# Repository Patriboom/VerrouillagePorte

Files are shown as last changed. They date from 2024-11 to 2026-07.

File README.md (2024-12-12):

# VerrouillagePorte
Verrouillage électronique d'une porte battante.  Projet basé sur programmation Arduino et module Rasp PI pico

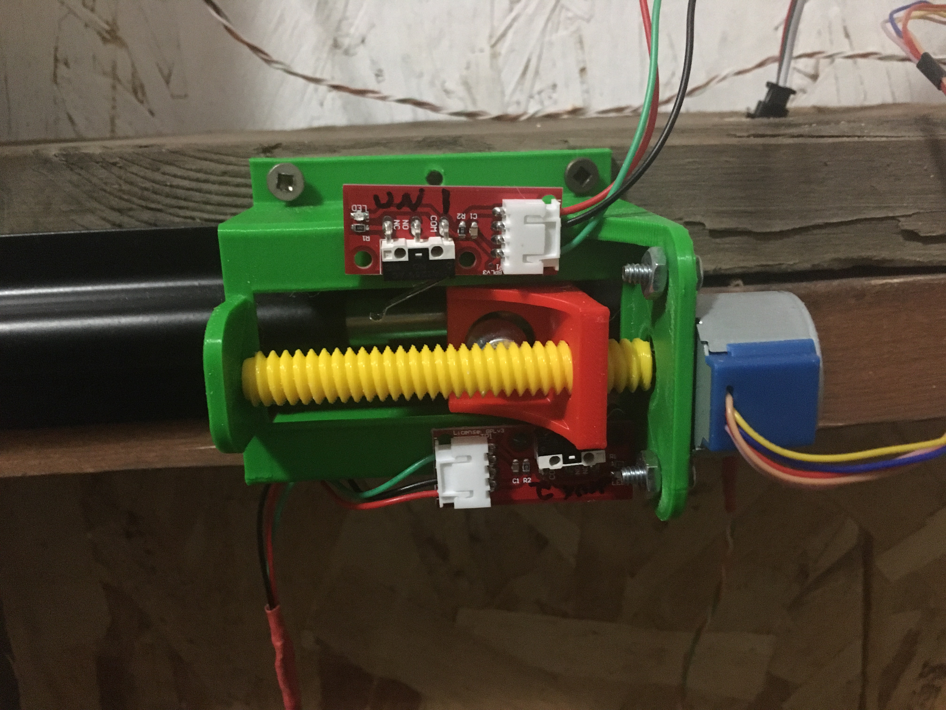
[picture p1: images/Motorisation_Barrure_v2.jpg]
Verrou installé
 Vue d`une installation fonctionnelle

Référez-vous à notre [tutoriel](https://github.com/Patriboom/VerrouillagePorte/tree/main/docs) :

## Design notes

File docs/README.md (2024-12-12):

# Bienvenue!

Dans ce tutoriel, je compte vous montrer comment j'ai imprimé, assemblé et programmé la fermeture et l'ouverture d'une verrou ordinaire qu'on trouve en quincaillerie.

Oui, vous pouvez acheter des produits tout faits, mais vous n'aurez pas la satisfaction de la réalisation personnelle, satisfaction qui me pousse aujourd'hui à vous partager mes fichiers et informations.

# Table des matières

1. [Introduction et présentation](01_Introduction_Presentation.md)
2. [Liste du matériel, des bibliothèques et des outils nécessaires](02_MaterielNecessaire.md)
3. [Le montage sur carte](03_Montage.md)
4. [Le câblage](04_Cablage.md)
5. [L'assemblage](05_Assemblage.md)
6. [Impression du support spécialisé](06_Impression_3d.md)
7. [La programmation](07_Programmation.md)
8. [Premier test et ajustements](08_PremierTest.md)
9. [Félicitations!](09_Felicitations.md)

Voici la pièce centrale du système: le support avec son moteur et ses pièces mobiles.
Verrou installé Vue d'une installation fonctionnelle

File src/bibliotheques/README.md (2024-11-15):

Attention, les bibliothèques fournies ici peuvent être désuètes.

Avec Arduino-IDE, vous trouverez les mêmes bibliothèques, mises à jour et entretenues par leurs auteurs.  Préférez cette option

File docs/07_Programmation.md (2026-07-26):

# 7. Programmation
La programmation est basée sur [Arduino](https://www.arduino.cc/).  L'outils ArduinoIDE est bien connu, répandu et docummenté.
Le code tout entier est disponible dans la banque de bibliothèques de ArduinoIDE.

Ici, je vous explique les différentes parties du code afin que vous puissiez le comprendre ou l'adapter à vos besoins.
Au travers du code, vous trouverez une foule de commentaires et même des repères et vérifications envoyés à la console afin que vous puissiez superviser la progression de la mise en oeuvre en direct.  Je ne reproduira pas ici les commentaires du code.

## Appel des bibliothèques nécessaires
```
	  #include <Stepper.h>
	  #include <SPI.h>
	  #include <MFRC522.h>
```

## Définition des variables de contrôle
```
	  int delai = 60000;
	  int pas = 20;
	  int sens = 1;
	  int vitesseMax = 700;
	  String libre = "oui";
	  bool tourne = false;
	  bool initOUV = false;
	  bool initFER = false;
	  int compteLOW = 0;
	  int compteDEL = 0;
	  int pinSW1 = 27;
	  int pinSW2 = 26;
	  int pinMO1 = 2;
	  int pinMO2 = 3;
	  int pinMO3 = 4;
	  int pinMO4 = 5;
	  int pinDER = 13;
	  int pinDEV = 14;
	  int pinDEB = 15;
	  int pinBOUT = 22;
	  byte CRT_RST = 21;
	  byte CRT_SSC = 17;
```

## Définition des variables de travail
```
 int rendu = 0;
```

## Création des objets
```
	  Stepper moteur(32, pinMO1, pinMO3, pinMO2, pinMO4);
	  MFRC522 cartes(CRT_SSC, CRT_RST);
```

## Définitions communes (setup)
```
	  void setup() {
	    Serial.begin(115200);
	    delay(1550);
	    Serial.println("");
	    Serial.println("Bonjour à vous; voici vos informations de suivi ... ");
	    SPI.begin();              // Init SPI bus
	    Serial.println("SPI est démarré.");
	    cartes.PCD_Init(); // Init each MFRC522 card
	    cartes.PCD_DumpVersionToSerial();
	    Serial.println("---------------------------------------");
	    pinMode(pinSW1, INPUT);   //Interrupteur fermé lorsque la porte est ouverte  => DEL vert
	    pinMode(pinSW2, INPUT);   //Interrupteur fermé lorsque la porte est fermée   => DEL rouge
	    pinMode(pinMO1, OUTPUT);  //Moteur 1
	    pinMode(pinMO2, OUTPUT);  //Moteur 2
	    pinMode(pinMO3, OUTPUT);  //Moteur 3
	    pinMode(pinMO4, OUTPUT);  //Moteur 4
	    pinMode(pinDER, OUTPUT);  //rouge de la DEL
	    pinMode(pinDEV, OUTPUT);  //vert de la DEL
	    pinMode(pinDEB, OUTPUT);  //bleu de la DEL
	    pinMode(pinBOUT, INPUT);
	    digitalWrite(pinMO1, LOW);
	    digitalWrite(pinMO2, LOW);
	    digitalWrite(pinMO3, LOW);
	    digitalWrite(pinMO4, LOW);
	    digitalWrite(pinDER, HIGH);
	    digitalWrite(pinDEV, HIGH);
	    digitalWrite(pinDEB, HIGH);
	    delay(1000);
	    if (digitalRead(pinSW1) == digitalRead(pinSW2)) {
	      Serial.println("Nous avons trouvé le verrou en position médiane; nous ouvrons la porte.");
	      mouvonsMoteur(-1, "fermons");
	    }
	    Serial.println("Voici que tout est défini.  Il ne reste qu`à jouer de la porte.");
	  }  // fin de setup()
```

## Traitement en boucle (loop)
```
	  void loop() {
	    rendu = rendu + 1;
	    if (rendu < 100 && libre == "oui") {
	      digitalWrite(pinDER, HIGH);
	      digitalWrite(pinDEV, LOW);
	      digitalWrite(pinDEB, LOW);
	    } else if (rendu < 200 && libre == "oui") {
	      digitalWrite(pinDER, HIGH);
	      digitalWrite(pinDEV, HIGH);
	      digitalWrite(pinDEB, LOW);
	    } else if (rendu < 300 && libre == "oui") {
	      digitalWrite(pinDER, LOW);
	      digitalWrite(pinDEV, HIGH);
	      digitalWrite(pinDEB, LOW);
	    } else if (rendu < 400 && libre == "oui") {
	      digitalWrite(pinDER, LOW);
	      digitalWrite(pinDEV, HIGH);
	      digitalWrite(pinDEB, HIGH);
	    } else if (rendu < 500 && libre == "oui") {
	      digitalWrite(pinDER, LOW);
	      digitalWrite(pinDEV, LOW);
	      digitalWrite(pinDEB, HIGH);
	    } else if (rendu < 600 && libre == "oui") {
	      digitalWrite(pinDER, HIGH);
	      digitalWrite(pinDEV, LOW);
	      digitalWrite(pinDEB, HIGH);
	    } else {
	      rendu = -1;
	      Serial.println("Nous voici en début de boucle.");
	    }
	    if (libre != "oui") { return; }
	    compteLOW = (digitalRead(pinBOUT) == HIGH) ? ++compteLOW : 0;
	    if (compteLOW > 10 ) { compteLOW = 0; mouvonsMoteur(0, ""); }
	    if ( (!cartes.PICC_IsNewCardPresent() || !cartes.PICC_ReadCardSerial())) {
	      return;
	    } else if (carteValide(cartes.uid.uidByte, cartes.uid.size)) {
	      mouvonsMoteur(0, "");
	    }
	  } //Fin de loop()
```

### Contrôle de la validité de la carte
```
	  bool carteValide(byte *buffer, byte bufferSize) {
	    Serial.print  ("Carte présente et lisible; voici sa valeur : ");
	    String pat = "";
	    for (byte i = 0; i < bufferSize; i++) {
	      pat = pat + String(buffer[i] < 0x10 ? " 0" : " ");
	      pat = pat + String(buffer[i], HEX);
	    }
	    pat.toUpperCase();
	    pat.trim();
	    if (pat == "") { Serial.println(" nulle."); return false; }
	    Serial.print  (pat);
	      for (byte i = 0; i < cartes.uid.size; i++) {
	        cartes.uid.uidByte[i] = 0;
	      }
	    if (pat=="89 A3 F0 97") { Serial.println(" (valide)."); return true; }
	    if (pat=="D3 B8 BD 38") { Serial.println(" (valide)."); return true; }
	    if (pat=="72 67 B1 AB") { Serial.println(" (valide)."); return true; }
	    Serial.println(" --- non valide.");
	    return false;
	  }
```

### Mouvement du moteur
```
	  void mouvonsMoteur(int Sens, String SensMvt) {
	    libre = (Sens == 0) ? "ouvrons" : SensMvt;
	    sens = (Sens == 0) ? 1 : Sens;
	    Serial.println("Activons les mouvements du moteur");
	    if (digitalRead(pinSW2) == LOW) {
	      sens = -1;
	      libre = "fermons";
	    }
	    digitalWrite(pinDER, HIGH);
	    digitalWrite(pinDEV, HIGH);
	    digitalWrite(pinDEB, HIGH);
	    if (Sens != 0) {
	        for (int x=0; x<5; x++) {
	            digitalWrite(pinDEB, LOW);
	            delay(250);
	            digitalWrite(pinDEB, HIGH);
	            delay(250);
	        }
	    }
	    Serial.print  ("État de la situation: ");
	    Serial.print  ((libre == "ouvrons") ? "Femeture demandée. " : "Ouverture demandée. ");
	    if (libre == "ouvrons") {
	      digitalWrite(pinDER, LOW);
	      digitalWrite(pinDEV, HIGH);
	    } else {
	      digitalWrite(pinDER, HIGH);
	        digitalWrite(pinDEV, LOW);
	    }
	    digitalWrite(pinDEB, LOW);
	    Serial.print  ("\tVitesse du moteur: ");
	    Serial.print  (vitesseMax);
	    Serial.print  ("\tPas du moteur: ");
	    Serial.println(pas);
	    int tours = 1;
	    int vitesse = 100;
	    //Mouvement
	    while (libre == "ouvrons" || libre == "fermons") {
	      if (tours/2500 == round(tours/2500) && vitesse < vitesseMax ) {
	        ////Accéléeration du moteur
	        vitesse = vitesse+50; moteur.setSpeed(vitesse);
	      }
	      ////Fin de course atteinte, on met un terme au movement.
	      if ((digitalRead(pinSW2) == LOW && libre == "ouvrons") || (digitalRead(pinSW1) == LOW && libre == "fermons")) {libre = "annoncons"; }
	      moteur.step(sens * pas);
	      delay(10);
	      tours=tours+1;
	    }
	    //Mise au repos du moteur
	    digitalWrite(pinMO1, LOW);
	    digitalWrite(pinMO2, LOW);
	    digitalWrite(pinMO3, LOW);
	    digitalWrite(pinMO4, LOW);
	    //Indication de l'état du verrou
	    digitalWrite(pinDER, HIGH);
	    digitalWrite(pinDEV, HIGH);
	    digitalWrite(pinDEB, HIGH);
	    for (int x=0; x<5; x++) {
	      if (digitalRead(pinSW1) == HIGH) {
	        ////La porte peut être ouverte
	        digitalWrite(pinDER, LOW);
	        Serial.println("Porte verrouilée; partez l`esprit tranquille, car votre porte est sécurisée.");
	      }
	      if (digitalRead(pinSW2) == HIGH) {
	        ////La porte est verrouillée
	        digitalWrite(pinDEV, LOW);
	        Serial.println("Porte déverrouillée; entrez!");
	      }
	      delay (250);
	      digitalWrite(pinDER, HIGH);
	      digitalWrite(pinDEV, HIGH);
	      delay (250);
	      libre = "oui";
	    }
	    delay(1900);
	    digitalWrite(pinDER, HIGH);
	    digitalWrite(pinDEV, HIGH);
	    digitalWrite(pinDEB, HIGH);
	    libre = "oui";
	  }
```

---
[Impression 3d](06_Impression_3d.md) <<<  [Table des matières](README.md)  >>>  [Premier test](08_PremierTest.md)

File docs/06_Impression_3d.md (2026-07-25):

# 6. Impression 3d en PLA
Le PLA est le plastique de base, celui avec lequel tous les apprentis font leurs premières expériences en impression 3d.  C'est un matériel abordable et convenant parfaitement à nos besoins.

## Description des pièces

## Logiciel de conception
Les pièces ici offertes ont été conçues à l'aide du logiciel [_FreeCad_](https://www.freecad.org/downloads.php)
Le fichier FreeCad suivant comprend toutes les pièces nécessaires:

[Fichiers FreeCad FCStd](../../../tree/main/imprime_3d/FreeCad/)
* [Motorisation_Barrure_v3](../../../tree/main/imprime_3d/FreeCad/Motorisation_Barrure_v3.FCStd)

## Tranchage (logiciel de préparation finale)

Les pièces ici présentées ont été préparée à l'aide du logiciel _Cura_
Les fichiers STL peuvent vous être utiles, mais ce serait étonnant car ils ont été générés spécifiquement pour une imprimante 3d. Or chaque imprimante a ses spécifications.
Il vous sera nécessire, donc, de générer vos propres fichiers STL à l'aide de votre logicition de tranchaage.

[Fichiers STL](../../../tree/main/imprime_3d/stl/)
* [Boulon](../../../tree/main/imprime_3d/stl/Motorisation_Barrure_v3-Boulon.stl)
* [Butoire](../../../tree/main/imprime_3d/stl/Motorisation_Barrure_v3-Butoir.stl)
* [Curseur](../../../tree/main/imprime_3d/stl/Motorisation_Barrure_v3-Curseur.stl)
* [Structure](../../../tree/main/imprime_3d/stl/Motorisation_Barrure_v3-Structure.stl)
* [Boitier_01](../../../tree/main/imprime_3d/stl/Obudowa.stl)
* [Boitier_02](../../../tree/main/imprime_3d/stl/Panel.stl)
* [Boitier_03](../../../tree/main/imprime_3d/stl/klapka.stl)

---

[L'assemblage](05_Assemblage.md)  <<<  [Table des matières](README.md)   >>>   [La programmation](07_Programmation.md)

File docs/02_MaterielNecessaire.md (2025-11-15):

# 2. Liste du matériel, des bibliothèques et outils nécessaires

## Électrique

<table>
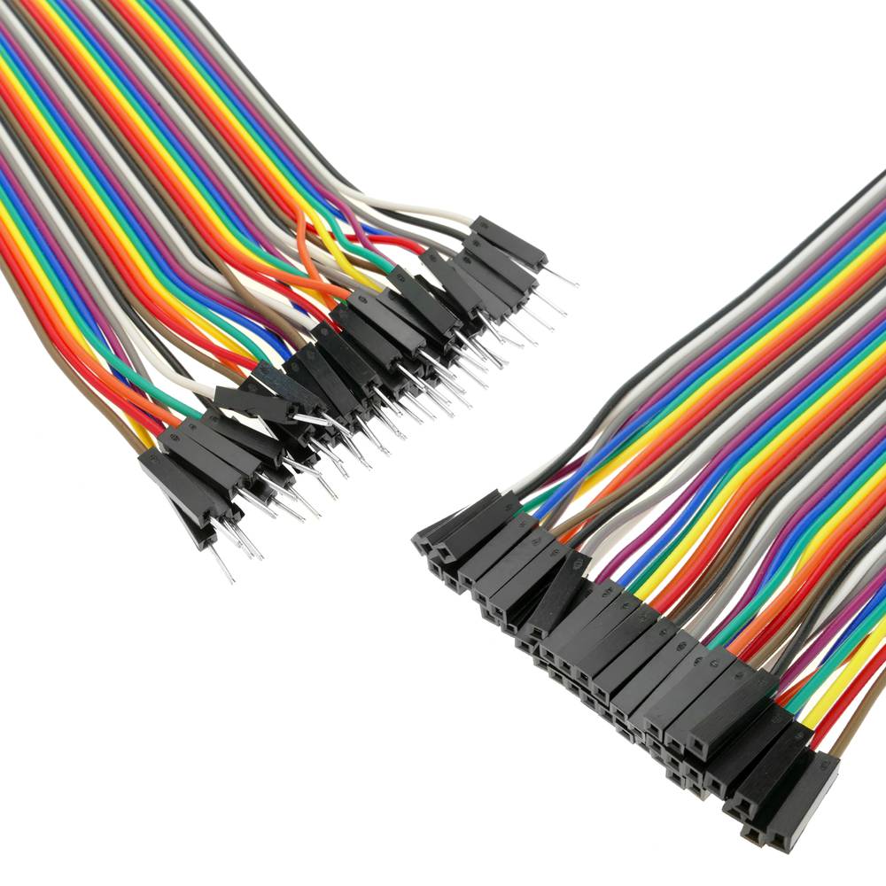
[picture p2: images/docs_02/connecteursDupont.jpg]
	<tr><td>Fils à connecteurs Dupont</td><td></td></tr>
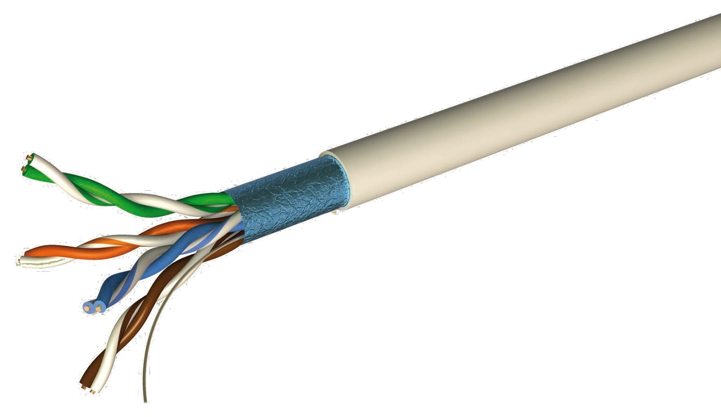
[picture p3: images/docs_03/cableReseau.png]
	<tr><td>Plusieurs sections de fil (un càble réseau peut fournir tout cela, en 8 couleurs)</td><td></td></tr>
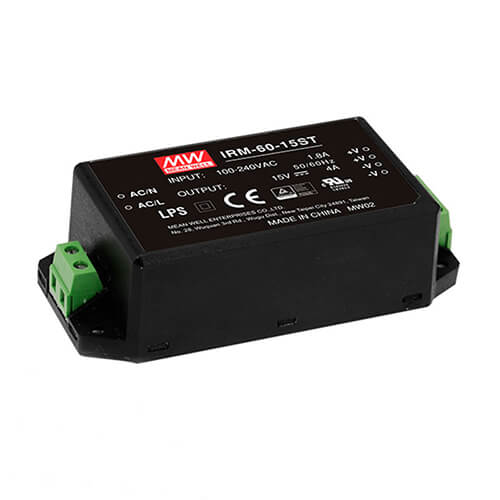
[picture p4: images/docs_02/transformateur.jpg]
	<tr><td>Transformateur 120 VAC -> 5 VDC</td><td></td></tr>
</table>

## Électronique

<table width="100%" border="0">
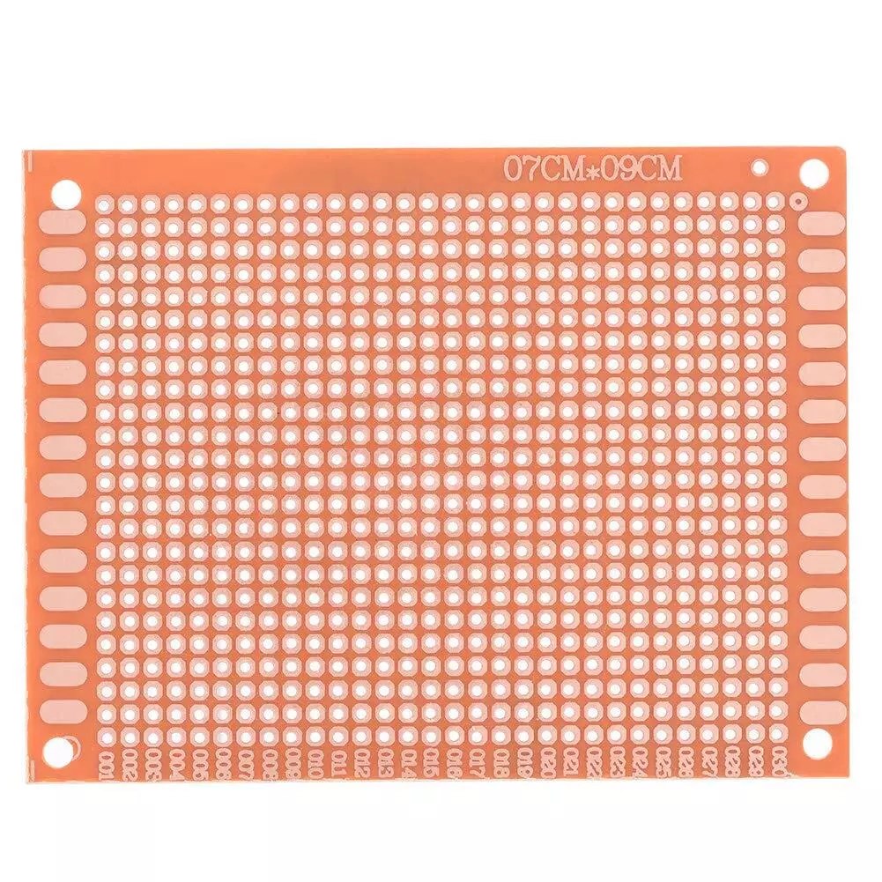
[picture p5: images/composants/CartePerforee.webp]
<tr><td></td><td>Carte perforée aux dimensions appropriées ( au moins 10 par 24 trous espacés de 2.54 mm)</td></tr>
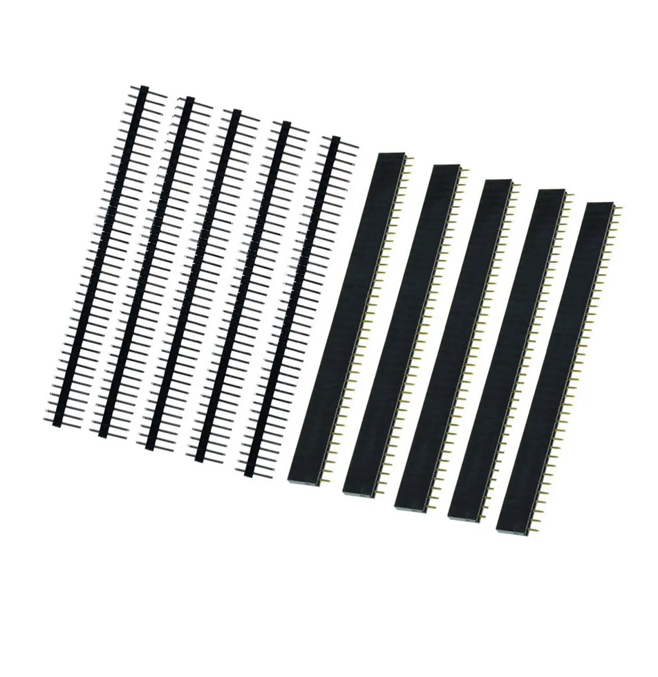
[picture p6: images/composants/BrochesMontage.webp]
<tr><td></td><td>Connecteurs mâles et femelles pour circuit imprimé</td></tr>
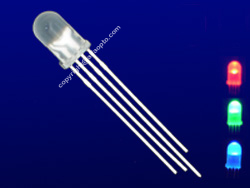
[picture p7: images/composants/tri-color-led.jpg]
<tr><td></td><td>DEL trois couleurs (RVB) à anode commune</td></tr>
<tr><td></td><td> Deux interrupteurs de limite</td></tr>
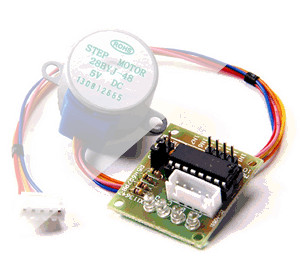
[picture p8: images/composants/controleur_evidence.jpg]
<tr><td> </td><td>Module de pilote de moteur pas à pas ULN2003</td></tr>
<tr><td>Image d'internet: Carte magnétique</td><td>Module RF5 RC522  (lecteur de cartes magnétiques)</td></tr>
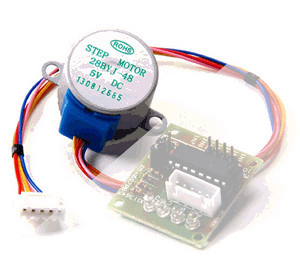
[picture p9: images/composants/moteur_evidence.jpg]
<tr><td></td><td>Moteur pas à pas 28BVJ-48 (5 Volts)</td></tr>
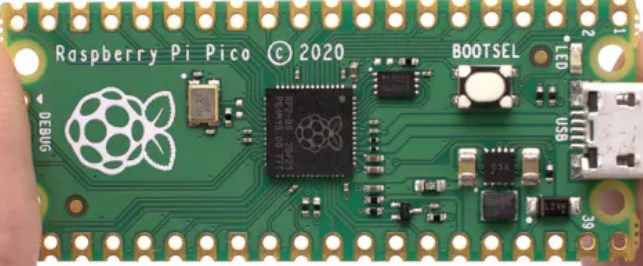
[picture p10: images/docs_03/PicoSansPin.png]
Image d`internet: Rasp PI pico
<tr><td></td><td>Raspberry PI Pico</td></tr>
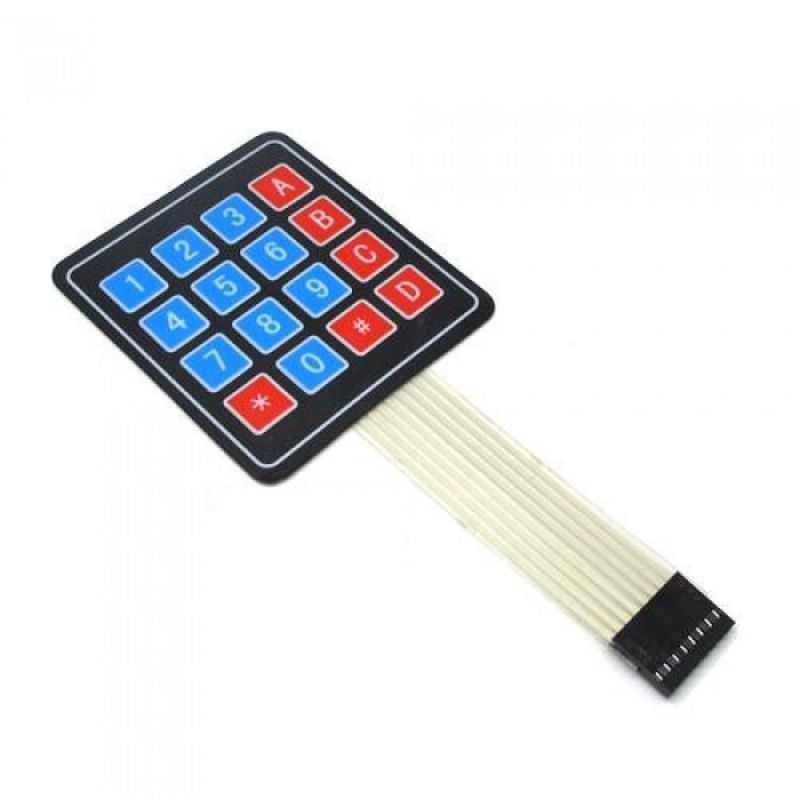
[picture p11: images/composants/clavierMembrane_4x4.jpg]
Image d'internet: Clavier à membrane
<tr><td></td><td>(option clavier à membrane) .. et oui ! ... le clavier à membrane</td></tr>

</table>

## Impression 3d
<table width="100%" border="0">
<tr><td colspan="2">Imprimer les quatre composantes du support en PLA</td></tr>
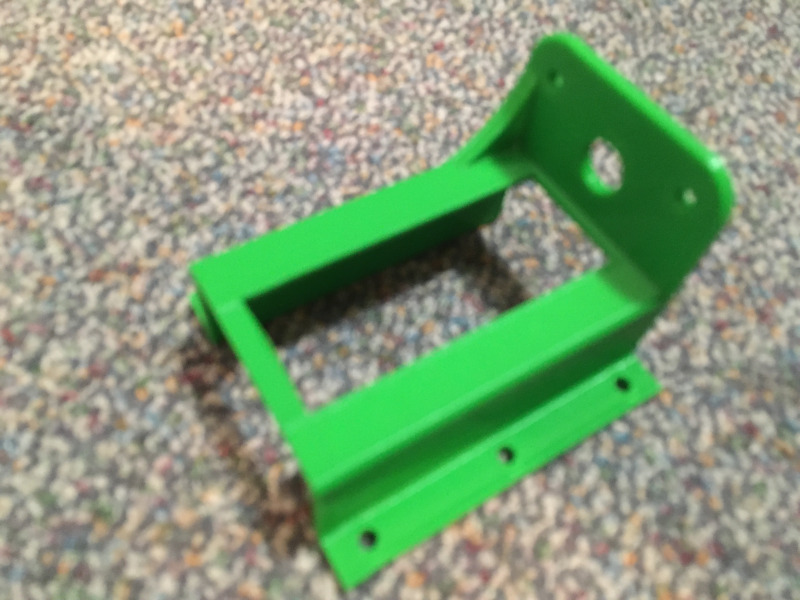
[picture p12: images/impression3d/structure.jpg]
	<tr><td>Une base (structure)</td><td></td></tr>
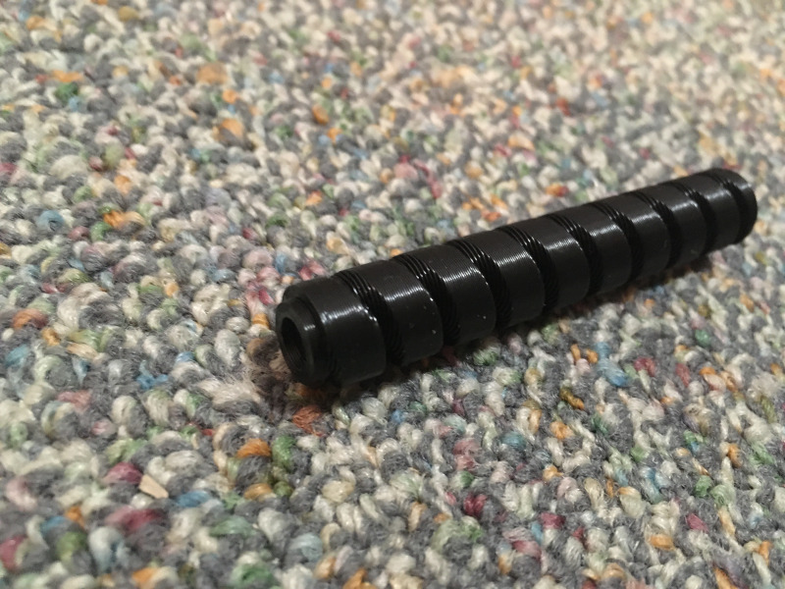
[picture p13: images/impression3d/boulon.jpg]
    <tr><td>Une vis sans fin (boulon)</td><td></td></tr>
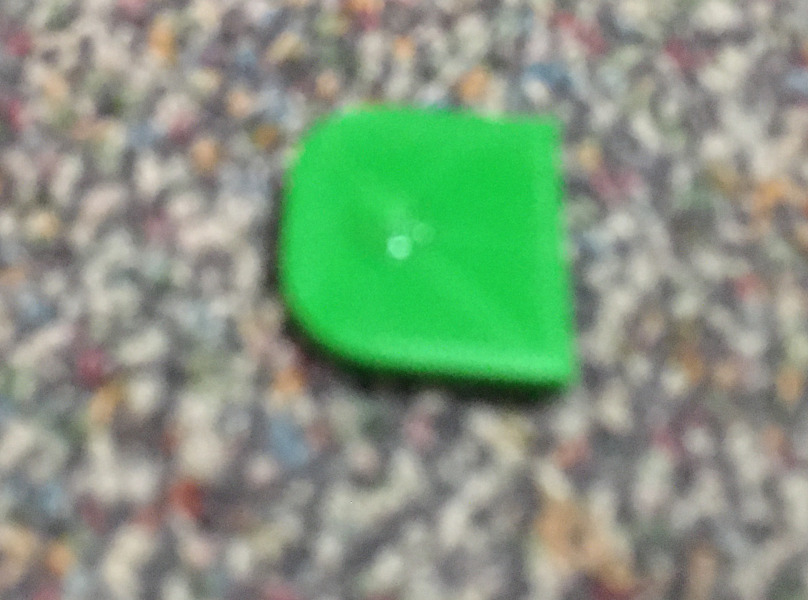
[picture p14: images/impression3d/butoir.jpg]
    <tr><td>Un butoir</td><td></td></tr>
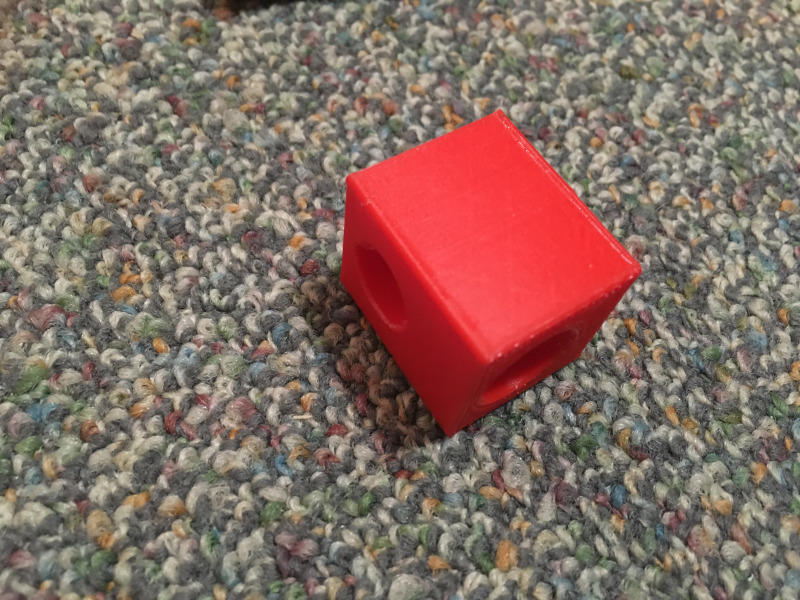
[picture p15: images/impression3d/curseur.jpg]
    <tr><td>Un curseur</td><td></td></tr>
</table>
<br />
<table width="100%" border="0">
<tr><td colspan="2">option: boîtier pour clavier en trois sections<br />C'est ici le modèle gratuitementt par <a href="https://cults3d.com/fr/mod%C3%A8le-3d/gadget/arduino-keypad-4x4-panel" target="_blank">kolec sur cults3d</a>
	</td></tr>
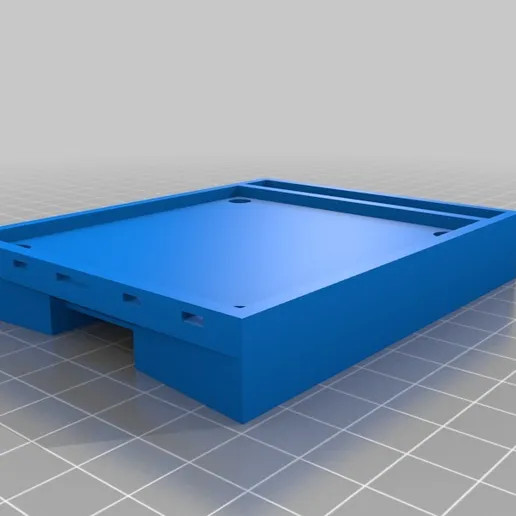
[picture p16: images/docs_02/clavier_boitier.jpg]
    <tr><td>Boîtier</td><td></td></tr>
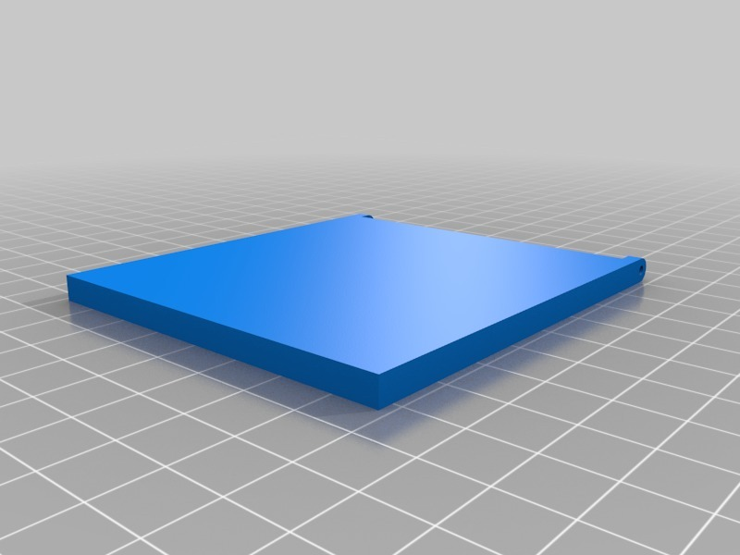
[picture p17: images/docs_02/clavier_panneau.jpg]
    <tr><td>Couvercle</td><td></td></tr>
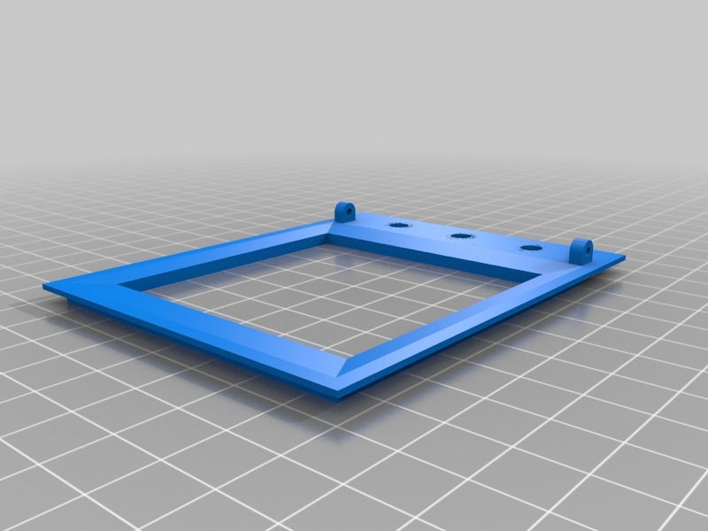
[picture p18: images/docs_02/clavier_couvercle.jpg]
	<tr><td>Dessus</td><td></td></tr>
</td></tr>
</table>

## Informatique
* Éditeur et compilateur de code [Arduino IDE](https://www.arduino.cc/en/software)
* [Bibliothèques installées](https://github.com/Patriboom/VerrouillagePorte/tree/main/src/bibliotheques):
    * Stepper.h
    * SPI.h
    * MFRC522.h
    * (pour l'option clavier à membrane): Keypad.h
* Pilote de carte: Raspberry PI Pico -> utilisez votre interface Arduino-IDE pour cela

## Mécanique
<table>
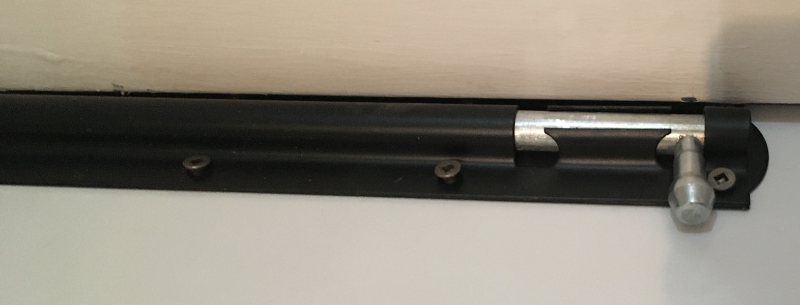
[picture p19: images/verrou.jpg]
<tr><td> </td><td>Verrou</td></tr>
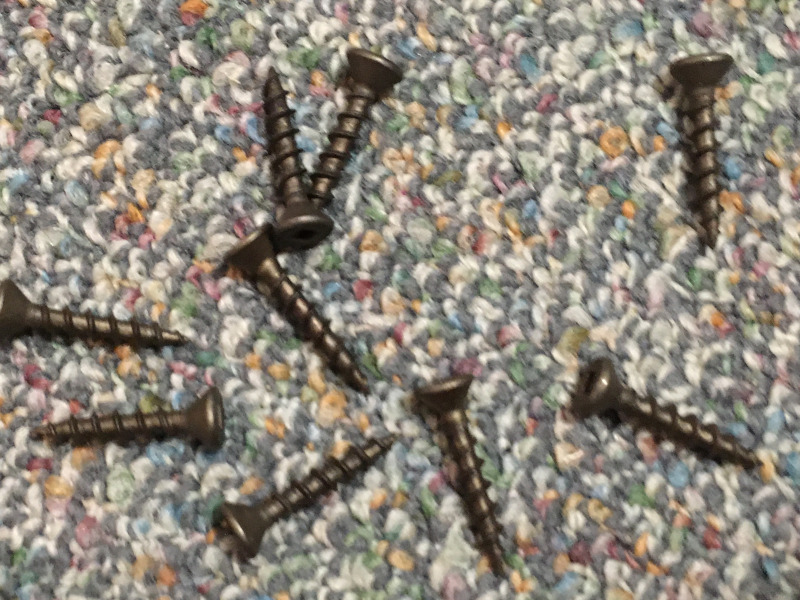
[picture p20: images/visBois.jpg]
<tr><td></td><td>Vis à bois</td></tr>
</table>

## Outils
<table>
	<tr><td></td><td>* Kit à souder  <br />
    &nbsp;&nbsp;&nbsp;&nbsp;&nbsp;&nbsp;- fer à souder <br />
	&nbsp;&nbsp;&nbsp;&nbsp;&nbsp;&nbsp;- étain<br />
		</td></tr>
<tr><td> </td><td>Perceuse & forêts à bois</td></tr>
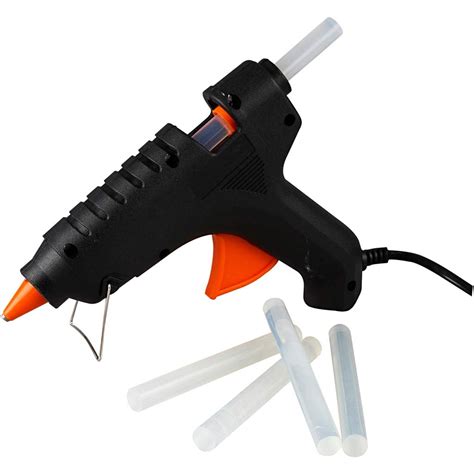
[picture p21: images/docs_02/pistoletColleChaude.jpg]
<tr><td></td><td>Pistolet à colle chaude et colle chaude</td></tr>
<tr></td><td><td>Tous les petits outils habituels permettant de couper et dégainer les fils</td></tr>
<tr><td></td><td>Tourne-vis</td></tr>
</table>

---

[Introduction](01_Introduction_Presentation.md)  <<<  [Table des matières](README.md)   >>>    [Montage](03_Montage.md)

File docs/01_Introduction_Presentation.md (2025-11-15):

# 1.Introduction et présentation du projet
Ma résidence dispose - heureusement en cas d'urgence! - de deux portes d'accès.  Une d'entre elles mène vers un espace commun.  Elle ne pouvait pas être verrouillée.  L'autre mène à l'extérieur et se verrouille à clef.  Cependant, l'installation laisse à désirer; il est facile de forcer la serrure et d'entrer.  Je l'ai d'ailleurs fait à quelques reprises lorsque j'ai oublié ma clef!  Je voulais donc plus de sécurité et la possibilité de me « forcer » à ne pas oublier ma clef avant de partir.

## Présentation

Ce projet a été réalisé avec les composants électroniques que j'avais sous la main.  Bien sûr, il pourrait être meilleur, plus beau ou plus performant, mais ce sont les composants dans je disposais qui ont été assemblés et réunis afin de réaliser une opération utile à la sécurisation de ma résidence.

Sans surprise, la sécurité étant ce qui est visé lors de l'ajout d'un verrou, la sécurité doit aussi être visée lors de sa motorisation.  L'image ci-bas montre les composants AVANT la finition esthétique de la porte, ceux-ci étant installés dans la structure même de la porte.
<br clear="all">

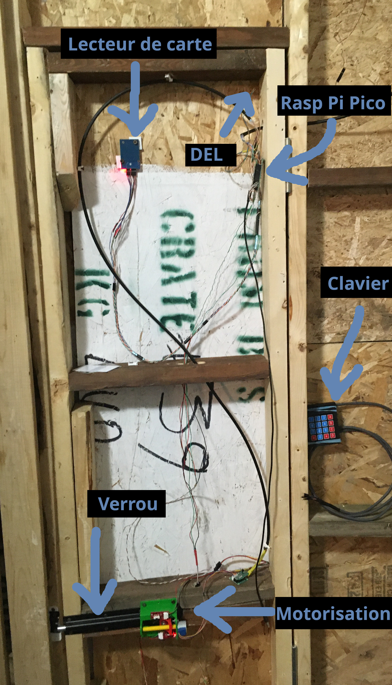
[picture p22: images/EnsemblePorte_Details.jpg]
Avant finition de la porte

<br clear="all">

## Fonctionnement
Ce système est basé sur un Raspberry Pi Pico qui gère l'activation d'un moteur par la lecture d'une carte magnétique.

Image d`internet: Rasp PI pico

Image d'internet: Carte magnétique

Image d'internet: moteur à pas
<br clear="all">
<br clear="all">
Le système est appelé à gérer aussi la vérification d'un code d'accès introduit à l'aide d'un clavier à membrane.
<br clear="all"><br />
Image d'internet: Clavier à membrane
<br clear="all"><br clear="all">
Le système électronique meut la barre d'un verrou en acier, barre d'environ 1cm de diamètre.

-----
[Table des matières](README.md)   >>>  [Le nécessaire](02_MaterielNecessaire.md)

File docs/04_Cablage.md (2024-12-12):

# 4. Le câblage

Prévoyez des câbles de bonne longueur pour chacun des éléments selon le positionnement de ceux-ci dans votre environnement.

De longueurs semblables, vous aurez: 
* Le contrôleur du moteur
* L'interrupteur de position « ouverte »
* L'interrupteur de position « verrouillée »

Quant aux autres, vous devrez composer avec l'environnement de votre installation.

Voici le schéma du câblage.
<br clear="all" />
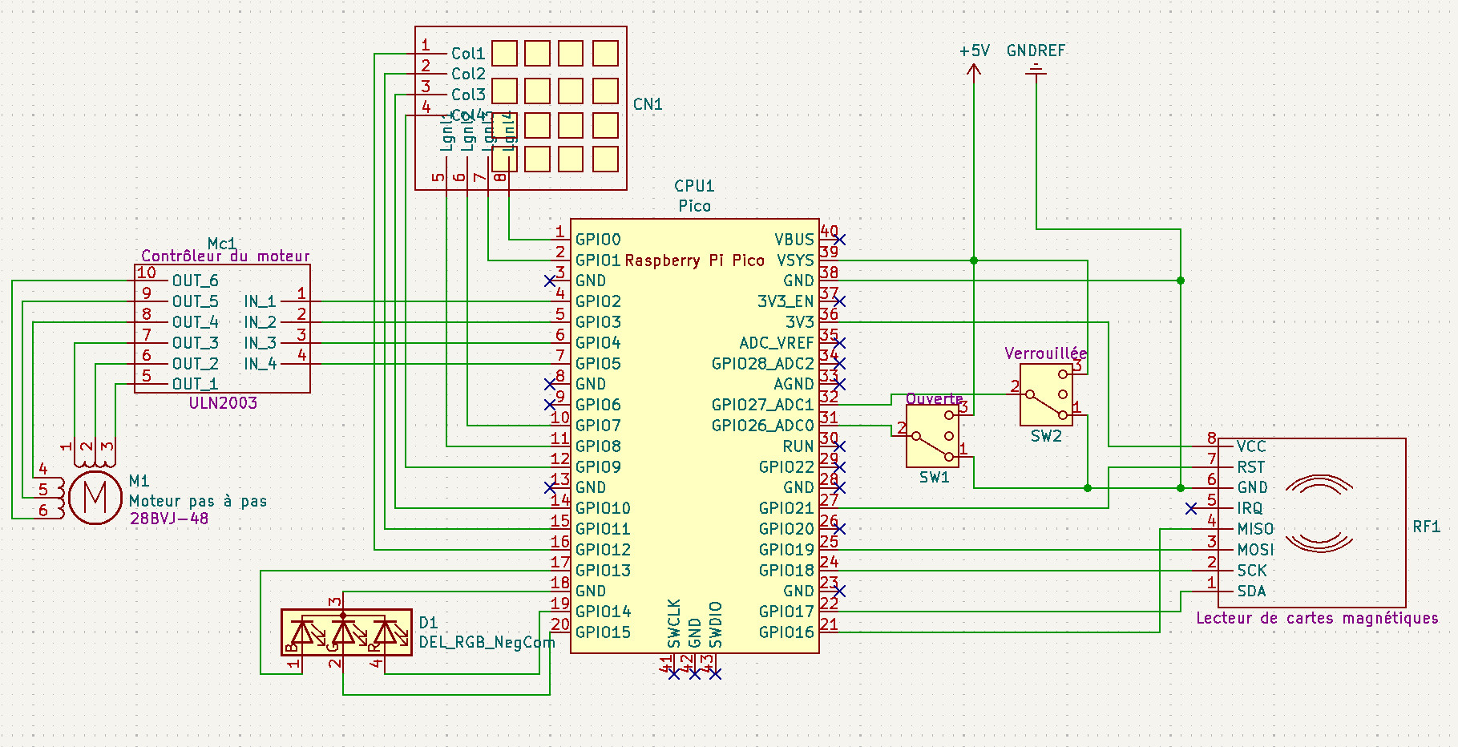
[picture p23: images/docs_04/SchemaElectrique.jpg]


---

[Montage du circuit](03_Montage.md)  <<<  [Table des matières](README.md)   >>>    [L'assemblage](05_Assemblage.md)

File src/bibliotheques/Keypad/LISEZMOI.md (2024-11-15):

# Keypad

Voici la petite bibliothèque servant à exploiter un clavier à membrane

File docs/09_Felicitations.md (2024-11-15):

# 9. Félicitations

---
[Premier test](08_PremierTest.md) <<<  [Table des matières](README.md)

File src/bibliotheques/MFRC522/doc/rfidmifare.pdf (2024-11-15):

## Using a MFRC522 reader to read and write MIFARE RFID cards

on ARDUINO through the MFRC522 library BY COOQROBOT.
Mario Capurso (m.capurso@libero.it)

MIFARE is the NXP Semiconductors-owned trademark of a series of chips widely
used in contactless smart cards and proximity cards. According to the producers, billions of smart card chips and many millions of reader modules have been sold. [1]

The technology is owned by NXP Semiconductors (spin off from Philips Electronics in 2006) with headquarters in Eindhoven, Netherlands, and main business sites in Nijmegen, Netherlands, and Hamburg, Germany.

The MIFARE name covers proprietary technologies based upon various levels of the ISO/IEC 14443 Type A 13.56 MHz contactless smart card standard.
The MIFARE name (derived from the term MIkron FARE Collection System) covers
seven different kinds of contactless cards.

MIFARE Classic employs a proprietary protocol compliant to parts (but not all) of ISO/IEC 14443-3 Type A, with an NXP proprietary security protocol for authentication and ciphering.

The MIFARE Classic card is fundamentally just a memory storage device, where the memory is divided into segments and blocks with simple security mechanisms for access control. They are ASIC-based and have limited computational power. Thanks
to their reliability and low cost, those cards are widely used for electronic wallet, access control, corporate ID cards, transportation or stadium ticketing.

The MIFARE Classic 1K offers 1024 bytes of data storage, split into 16 sectors; each sector is protected by two different keys, called A and B. Each key can be programmed to allow operations such as reading, writing, increasing valueblocks, etc. MIFARE Classic 4K offers 4096 bytes split into forty sectors, of which 32 are same size as in the 1K with eight more that are quadruple size sectors. MIFARE Classic mini offers 320 bytes split into five sectors.

For each of these card types, 16 bytes per sector are reserved for the keys and access conditions and can not normally be used for user data. Also, the very first 16 bytes contain the serial number of the card and certain other manufacturer data and are read only. That brings the net storage capacity of these cards down to 752 bytes for MIFARE Classic 1k, 3440 bytes for MIFARE Classic 4k, and 224 bytes for Mini. It uses an NXP proprietary security protocol (Crypto-1) for authentication and ciphering.

The encryption used by the MIFARE Classic card uses a 48 bit key. [18]
A presentation by Henryk Plötz and Karsten Nohl[19] at the Chaos Communication Congress in December 2007 described a partial reverse-engineering of the algorithm used in the MIFARE Classic chip. Abstract and slides[20] are available online. A paper that describes the process of reverse engineering this chip was published at the August 2008 USENIX security conference.[21] (https://www.usenix.org/legacy/events/sec08/tech/full_papers/nohl/nohl.pdf)

In March 2008 the Digital Security[22] research group of the Radboud University Nijmegen made public that they performed a complete reverse-engineering and
were able to clone and manipulate the contents of an OV-Chipkaart which is a MIFARE Classic card.[23] (http://www.cs.ru.nl/~flaviog/publications/Talk.Mifare.pdf) For demonstration they used the Proxmark device, a 125 kHz / 13.56 MHz research instrument.[24] The schematics and software are released under the free GNU General Public License by Jonathan Westhues in 2007. They demonstrate it is even possible to perform card-only attacks using just an ordinary stock-commercial NFC reader in combination with the libnfc library.

In April 2009 new and better card-only attack on MIFARE Classic has been
found. It was first announced at the Rump session of Eurocrypt 2009.[35] This attack was presented at SECRYPT 2009.[36] The full description of this latest and fastest attack to date can also be found in the IACR preprint archive.[37] The new attack improves by a factor of more than 10 all previous card-only attacks on MIFARE Classic, has instant running time, and it does not require a costly precomputation.

The new attack allows to recover the secret key of any sector of MIFARE Classic card via wireless interaction, within about 300 queries to the card. It can then be combined with the nested authentication attack in the Nijmegen Oakland paper to recover subsequent keys almost instantly. Both attacks combined and with the right hardware equipment such as Proxmark3, one should be able to clone any MIFARE Classic card in not more than 10 seconds. This is much faster than previously thought.

The MFRC522 is a highly integrated reader/writer IC for contactless communication at 13.56 MHz. The MFRC522 reader supports ISO/IEC 14443 A/MIFARE mode.
The MFRC522’s internal transmitter is able to drive a reader/writer antenna designed to communicate with ISO/IEC 14443 A/MIFARE cards and transponders without additional active circuitry. The receiver module provides a robust and efficient implementation for demodulating and decoding signals from ISO/IEC 14443 A/MIFARE compatible cards and transponders. The digital module manages the complete ISO/IEC 14443 A framing and error detection (parity and CRC) functionality.

The MFRC522 supports all variants of the MIFARE Mini, MIFARE 1K, MIFARE 4K, MIFARE Ultralight, MIFARE DESFire EV1 and MIFARE Plus RF identification protocols. To aid readability throughout this data sheet, the MIFARE Mini,

MIFARE 1K, MIFARE 4K, MIFARE Ultralight, MIFARE DESFire EV1 and MIFARE Plus products and protocols have the generic name MIFARE.

The following host interfaces are provided:

- Serial Peripheral Interface (SPI)
- Serial UART (similar to RS232 with voltage levels dependant on pin voltage supply)
- I2C-bus interface

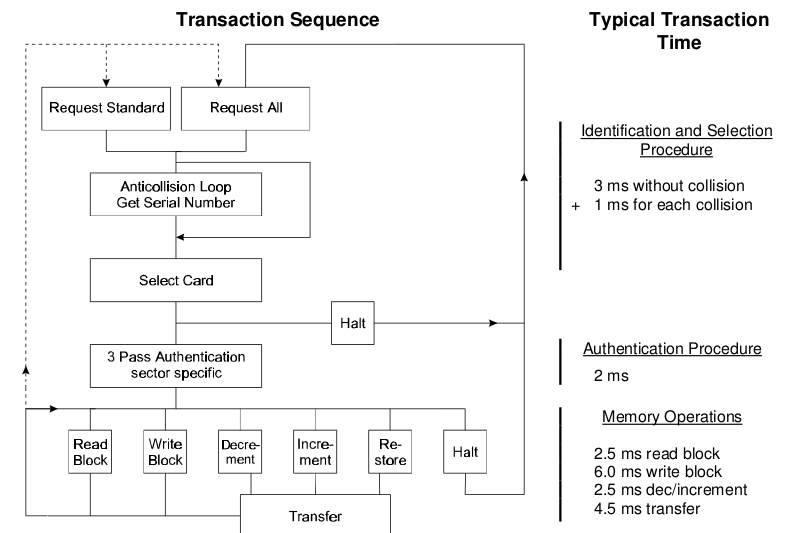
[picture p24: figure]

Answer to Request :

With the Answer to Request sequence the MIFARE® RWD (Read Write Device) requests all MIFARE® cards in the antenna field. When a card is in the operating range of a RWD, the RWD continues communication with the appropriate protocol.

Anticollision loop
In the Anticollision loop the serial number of the card is read. If there are several cards in the operating range of a RWD they can be distinguished by their different serial numbers and one can be selected (Select card) for further transactions. The unselected cards return to the standby mode and wait for a new Answer to Request and Anticollision loop.

Select Card
With the Select Card command the RWD selects one individual card for further authentication and memory related operations. The card returns the Answer to Select (ATS) code, which determines the individual type of the selected card.

Access Specification
After identification and selection of one card the RWD specifies the memory location of the following access.

Three Pass Authentication
The appropriate access key for the previously specified access is used for 3 Pass Authentication. Any communication after authentication is automatically encrypted at the sender and decrypted by the receiver.

Read/Write

After authentication any of the following operations may be performed:

READ | reads one block
WRITE | writes one block
DECREMENT | decrements the contents of one block and stores the result
| in the data-register
INCREMENT | increments the contents of one block and stores the result
| in the data-register
TRANSFER | writes the contents of the data-register to one block
RESTORE | stores the contents of one block in the data-register

The MF1ICS50 IC of a Mifare Classic has integrated a 8192 Bit EEPROM which is split into 16 sectors with 4 blocks. One block consists of 16 bytes (1 Byte = 8 Bit).

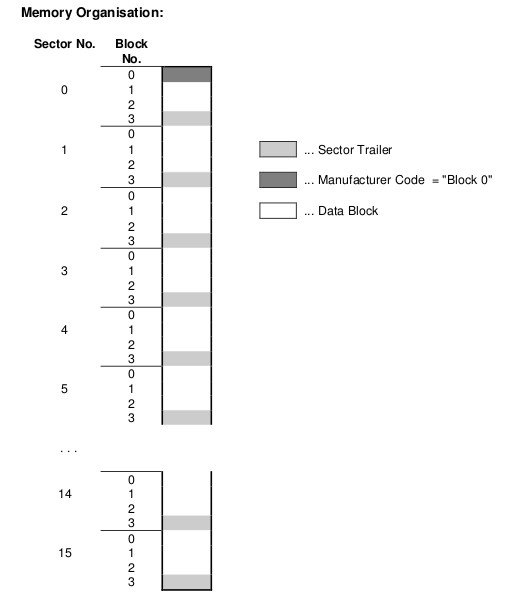
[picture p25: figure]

Manufacturer Code (Block 0 of Sector 0)

The first block of the memory is reserved for manufacturer data like 32 bit serial number. This is a read only block. In many documents it is named "Block 0".

Data Block (Block 0 to 3 except "Block 0")

Access conditions for the Data Blocks are defined in the Sector Trailers. According to these conditions data can be read, written, incremented, decremented, transferred or restored either with Key A, Key B or never.


If Key B may be read in the corresponding Sector Trailer it cannot serve for authentication (all grey marked lines in previous table). Consequences: If the RWD tries to authenticate any block of a sector with key B using grey marked
access conditions, the card will refuse any subsequent memory access after authentication


The described memory organization makes it possible to appoint different sectors to different applications and to prevent data corruption by using application specific secret keys. Keys can only be altered by a RWD which has stored the actual Key A or Key B if this is allowed according to access conditions. Otherwise the actual key cannot be changed anymore.

Before the execution of a command the correct format of the Access Conditions is checked by the Card-IC. Thus, when programming the Sector Trailer the card needs to be fixed within the operating range of a RWD's antenna to prevent interruption of the write operation because any unsuccessful write operation may lead to blocking the whole sector.


## MFRC522.h – A Library to use ARDUINO RFID MODULE KIT 13.56

MHZ BY COOQROBOT.

There are three hardware components involved:

1) The micro controller: An Arduino
2) The PCD (Proximity Coupling Device): NXP MFRC522 Contactless Reader IC
3) The PICC (short for Proximity Integrated Circuit Card): A card or tag using the ISO 14443A interface, eg Mifare or NTAG203.

MIFARE Classic 1K (MF1S503x):

Has 16 sectors * 4 blocks/sector * 16 bytes/block = 1024 bytes. The blocks are numbered 0-63.

Block 3 in each sector is the Sector Trailer.
* | Bytes 0-5: | Key A
* | Bytes 6-8: | Access Bits
* | Bytes 9: | User data
* | Bytes 10-15: Key B (or user data)

Block 0 is read only manufacturer data.

To access a block, an authentication using a key from the block's sector must be performed first.

Example: To read from block 10, first authenticate using a key from sector 3 (blocks 8-11).

All keys are set to FFFFFFFFFFFFh at chip delivery.

Warning: Please read section 8.7 "Memory Access". It includes this text: if the PICC detects a format violation the whole sector is irreversibly blocked.

To use a block in "value block" mode (for Increment/Decrement operations) you need to change the sector trailer. Use PICC_SetAccessBits() to calculate the bit patterns.

Commands sent to the PICC.

The commands used by the PCD to manage communication with several PICCs (ISO 14443-3, Type A, section 6.4)

PICC_CMD_REQA = 0x26,
REQuest command, Type A. Invites PICCs in state IDLE to go to READY and prepare for anticollision or selection. 7 bit frame.
PICC_CMD_WUPA = 0x52,
Wake-UP command, Type A. Invites PICCs in state IDLE and HALT to go to READY(*) and prepare for anticollision or selection. 7 bit frame.
PICC_CMD_CT = 0x88,
Cascade Tag. Not really a command, but used during anti collision. PICC_CMD_SEL_CL1 = 0x93,
Anti collision/Select, Cascade Level 1
PICC_CMD_SEL_CL2 = 0x95,
Anti collision/Select, Cascade Level 2 PICC_CMD_SEL_CL3 = 0x97,
Anti collision/Select, Cascade Level 3
PICC_CMD_HLTA = 0x50,
HaLT command, Type A. Instructs an ACTIVE PICC to go to state HALT.

The commands used for MIFARE Classic
Use PCD_MFAuthent to authenticate access to a sector, then use these commands to read/write/modify the blocks on the sector.
The read/write commands can also be used for MIFARE Ultralight.

PICC_CMD_MF_AUTH_KEY_A = 0x60,
Perform authentication with Key A
PICC_CMD_MF_AUTH_KEY_B = 0x61,
Perform authentication with Key B
PICC_CMD_MF_READ | = 0x30,
Reads one 16 byte block from the authenticated sector of the PICC. Also used for MIFARE Ultralight.
PICC_CMD_MF_WRITE | = 0xA0,
Writes one 16 byte block to the authenticated sector of the PICC. Called "COMPATIBILITY WRITE" for MIFARE Ultralight.
PICC_CMD_MF_DECREMENT = 0xC0,
Decrements the contents of a block and stores the result in the internal data register.
PICC_CMD_MF_INCREMENT = 0xC1,
Increments the contents of a block and stores the result in the internal data register.
PICC_CMD_MF_RESTORE | = 0xC2,
Reads the contents of a block into the internal data register. PICC_CMD_MF_TRANSFER = 0xB0,
Writes the contents of the internal data register to a block.

List of the functions in the library

Functions for setting up the Arduino

MFRC522(byte chipSelectPin, byte resetPowerDownPin);
void setSPIConfig();

Basic interface functions for communicating with the MFRC522

void PCD_WriteRegister(byte reg, byte value);
void PCD_WriteRegister(byte reg, byte count, byte *values);
byte PCD_ReadRegister(byte reg);
void PCD_ReadRegister(byte reg, byte count, byte *values, byte rxAlign = 0); void setBitMask(unsigned char reg, unsigned char mask);
void PCD_SetRegisterBitMask(byte reg, byte mask);
void PCD_ClearRegisterBitMask(byte reg, byte mask);
byte PCD_CalculateCRC(byte *data, byte length, byte *result);

Functions for manipulating the MFRC522

void PCD_Init();
void PCD_Reset();
void PCD_AntennaOn();

Functions for communicating with PICCs

byte PCD_TransceiveData(byte *sendData, byte sendLen, byte *backData, byte *backLen, byte *validBits = NULL, byte rxAlign = 0, bool checkCRC = false);

byte PCD_CommunicateWithPICC(byte command, byte waitIRq, byte *sendData, byte sendLen, byte *backData = NULL, byte *backLen = NULL, byte *validBits = NULL, byte rxAlign = 0, bool checkCRC = false);

byte PICC_RequestA(byte *bufferATQA, byte *bufferSize);
byte PICC_WakeupA(byte *bufferATQA, byte *bufferSize);
byte PICC_REQA_or_WUPA( byte command, byte *bufferATQA, byte *bufferSize); byte PICC_Select(Uid *uid, byte validBits = 0);
byte PICC_HaltA();

Functions for communicating with MIFARE PICCs

byte PCD_Authenticate(byte command, byte blockAddr, MIFARE_Key *key, Uid *uid); void PCD_StopCrypto1();
byte MIFARE_Read(byte blockAddr, byte *buffer, byte *bufferSize);
byte MIFARE_Write(byte blockAddr, byte *buffer, byte bufferSize);
byte MIFARE_Decrement(byte blockAddr, long delta);
byte MIFARE_Increment(byte blockAddr, long delta);
byte MIFARE_Restore(byte blockAddr);
byte MIFARE_Transfer(byte blockAddr);
byte MIFARE_Ultralight_Write(byte page, byte *buffer, byte bufferSize);

Support functions

byte PCD_MIFARE_Transceive( byte *sendData, byte sendLen, bool acceptTimeout = false);
const char *GetStatusCodeName(byte code);
byte PICC_GetType(byte sak);
const char *PICC_GetTypeName(byte type);
void PICC_DumpToSerial(Uid *uid);
void PICC_DumpMifareClassicToSerial(Uid *uid, byte piccType, MIFARE_Key *key);
void PICC_DumpMifareClassicSectorToSerial(Uid *uid, MIFARE_Key *key, byte sector); void PICC_DumpMifareUltralightToSerial();
void MIFARE_SetAccessBits(byte *accessBitBuffer, byte g0, byte g1, byte g2, byte g3);

Convenience functions - does not add extra functionality

bool PICC_IsNewCardPresent();
bool PICC_ReadCardSerial();

Detailed documentation – enum and structures

PICC types we can detect. Remember to update PICC_GetTypeName() if you add more.

enum PICC_Type

Return codes from the functions in this class. Remember to update GetStatusCodeName() if you add more.

enum StatusCode

A struct used for passing the UID of a PICC.

typedef struct {
byte | size; | Number of bytes in the UID. 4, 7 or 10.
byte | uidByte[10];
byte | sak; | The SAK (Select acknowledge) byte returned
| | from the PICC after successful selection.
} Uid

A struct used for passing a MIFARE Crypto1 key

typedef struct {
byte | keyByte[MF_KEY_SIZE];
} MIFARE_Key;

Example:
// Prepare key - all keys are set to FFFFFFFFFFFFh at chip delivery from the factory. MFRC522::MIFARE_Key key;
for (byte i = 0; i < 6; i++) key.keyByte[i] = 0xFF;

Member variables

Uid uid; | Used by PICC_ReadCardSerial().

Detailed documentation – functions

+Create object instance
MFRC522(
byte chipSelectPin, Arduino pin used for SPI chip select byte resetPowerDownPin Arduino pin used for SPI reset
);
Example:
#include <SPI.h>

#include <MFRC522.h>

#define SS_PIN 10 //Arduino Uno

#define RST_PIN 9

MFRC522 mfrc522(SS_PIN, RST_PIN); | // Create MFRC522 instance.

+Initializes the MFRC522 chip.
void MFRC522::PCD_Init()
Example:
void setup() {
Serial.begin(9600); | // Init serial communications with PC
SPI.begin(); | // Init SPI bus
mfrc522.PCD_Init(); | // Init MFRC522 card
}

+Set SPI bus to work with MFRC522 chip.

Please call this function if you have changed the SPI config since the MFRC522 constructor was run.

void MFRC522::setSPIConfig()

+Performs a soft reset on the MFRC522 chip and waits for it to be ready again. void MFRC522::PCD_Reset()

+Turns the antenna on by enabling pins TX1 and TX2.
After a reset these pins are disabled.
void MFRC522::PCD_AntennaOn()

+Transmits a REQuest command, Type A. Invites PICCs in state IDLE to go to READY and prepare for anticollision or selection. 7 bit frame.
Beware: When two PICCs are in the field at the same time I often get STATUS_TIMEOUT -probably due do bad antenna design.
return STATUS_OK on success, STATUS_??? otherwise.
byte MFRC522::PICC_RequestA(
byte *bufferATQA, The buffer to store the ATQA (Answer to request) in
byte *bufferSize Buffer size, at least two bytes. Also number of bytes returned if STATUS_OK.

+Transmits a Wake-UP command, Type A. Invites PICCs in state IDLE and HALT to go to READY(*) and prepare for anticollision or selection. 7 bit frame.
Beware: When two PICCs are in the field at the same time I often get STATUS_TIMEOUT -probably due do bad antenna design.
return STATUS_OK on success, STATUS_??? otherwise.
byte MFRC522::PICC_WakeupA(
byte *bufferATQA, The buffer to store the ATQA (Answer to request) in
byte *bufferSize Buffer size, at least two bytes. Also number of bytes returned if STATUS_OK.

+Transmits SELECT/ANTICOLLISION commands to select a single PICC.
Before calling this function the PICCs must be placed in the READY(*) state by calling PICC_RequestA() or PICC_WakeupA().
On success:

-The chosen PICC is in state ACTIVE(*) and all other PICCs have returned to state IDLE/HALT. (Figure 7 of the ISO/IEC 14443-3 draft.)
-The UID size and value of the chosen PICC is returned in *uid along with the SAK.

A PICC UID consists of 4, 7 or 10 bytes.
Only 4 bytes can be specified in a SELECT command, so for the longer UIDs two or three iterations are used:
UID size | Number of UID bytes | Cascade levels | Example of PICC
======== | =================== | ============== | ===============
single | 4 | 1 | MIFARE Classic
double | 7 | 2 | MIFARE Ultralight
triple | 10 | 3 | Not currently in use?

return STATUS_OK on success, STATUS_??? otherwise.
byte MFRC522::PICC_Select(
Uid *uid, | Pointer to Uid struct. Normally output, but can also
be used to supply a known UID.
byte validBits | The number of known UID bits supplied in *uid.

Normally 0. If set you must also supply uid->size.

Description of buffer structure:

Byte 0: SEL | Indicates the Cascade Level: PICC_CMD_SEL_CL1,
PICC_CMD_SEL_CL2 or PICC_CMD_SEL_CL3
Byte 1: NVB | Number of Valid Bits (in complete command, not just the UID):
High nibble: complete bytes, Low nibble: Extra bits.
Byte 2: UID-data or CT See explanation below. CT means Cascade Tag.
Byte 3: UID-data
Byte 4: UID-data
Byte 5: UID-data
Byte 6: BCC | Block Check Character - XOR of bytes 2-5
Byte 7: CRC_A
Byte 8: CRC_A

The BCC and CRC_A is only transmitted if we know all the UID bits of the current Cascade Level.
Description of bytes 2-5: (Section 6.5.4 of the ISO/IEC 14443-3 draft: UID contents and cascade levels)
UID size | Cascade level | Byte2 Byte3 Byte4 Byte5
======== | ============= | ===== ===== ===== =====
4 bytes | 1 | uid0 uid1 uid2 uid3

7 bytes | 1 | CT | uid0 uid1 uid2
2 | uid3 uid4 uid5 uid6
10 bytes | 1 | CT | uid0 uid1 uid2
| 2 | CT | uid3 uid4 uid5

+Instructs a PICC in state ACTIVE(*) to go to state HALT. return STATUS_OK on success, STATUS_??? otherwise.
byte PICC_HaltA();
Example:
// Halt PICC
mfrc522.PICC_HaltA();

+Executes the MFRC522 MFAuthent command.
This command manages MIFARE authentication to enable a secure communication to any MIFARE Mini, MIFARE 1K and MIFARE 4K card.
The authentication is described in the MFRC522 datasheet section 10.3.1.9 and http://www.nxp.com/documents/data_sheet/MF1S503x.pdf section 10.1. for use with MIFARE Classic PICCs.
The PICC must be selected - ie in state ACTIVE(*) - before calling this function. Remember to call PCD_StopCrypto1() at the end of communication with the authenticated PICC - otherwise no new communications can start.
All keys are set to FFFFFFFFFFFFh at chip delivery.
return STATUS_OK on success, STATUS_??? otherwise. Probably STATUS_TIMEOUT if you supply the wrong key.
byte MFRC522::PCD_AuthenticateI(
byte command, | PICC_CMD_MF_AUTH_KEY_A or PICC_CMD_MF_AUTH_KEY_B
byte blockAddr, | The block number. See numbering in the comments in
| the .h file.
MIFARE_Key *key, | Pointer to the Crypto1 key to use (6 bytes)
Uid *uid | Pointer to Uid struct. The first 4 bytes of the UID
| is used.
)
Example:
MFRC522::MIFARE_Key key;
for (byte i = 0; i < 6; i++) key.keyByte[i] = 0xFF; byte trailerBlock = 7;
byte status;
if ( ! mfrc522.PICC_ReadCardSerial()) return;
status = mfrc522.PCD_Authenticate(MFRC522::PICC_CMD_MF_AUTH_KEY_A, trailerBlock, &key, &(mfrc522.uid));
if (status != MFRC522::STATUS_OK) {
Serial.print("PCD_Authenticate() failed: "); Serial.println(mfrc522.GetStatusCodeName(status)); return;
}

+Used to exit the PCD from its authenticated state.
Remember to call PCD_StopCrypto1() at the end of communication with the authenticated PICC - otherwise no new communications can start.
void MFRC522::PCD_StopCrypto1()
Example:
// Stop encryption on PCD
mfrc522.PCD_StopCrypto1();

+Reads 16 bytes (+ 2 bytes CRC_A) from the active PICC.
For MIFARE Classic the sector containing the block must be authenticated before calling this function.
For MIFARE Ultralight only addresses 00h to 0Fh are decoded.
* The MF0ICU1 returns a NAK for higher addresses.

* The MF0ICU1 responds to the READ command by sending 16 bytes starting from
the page address defined by the command argument.
* For example; if blockAddr is 03h then pages 03h, 04h, 05h, 06h are returned.
* A roll-back is implemented: If blockAddr is 0Eh, then the contents of pages 0Eh, 0Fh, 00h and 01h are returned.
The buffer must be at least 18 bytes because a CRC_A is also returned.
Checks the CRC_A before returning STATUS_OK.
return STATUS_OK on success, STATUS_??? otherwise.
byte MFRC522::MIFARE_Read(
byte blockAddr, | MIFARE Classic: The block (0-0xff) number.
| MIFARE Ultralight: The first page to return data from.
byte *buffer, | The buffer to store the data in

byte *bufferSize Buffer size, at least 18 bytes. Also number of bytes returned
| if STATUS_OK.
Example:
byte valueBlockA = 4; byte buffer[18]; byte size = sizeof(buffer);
byte status = mfrc522.MIFARE_Read(valueBlockA, buffer, &size);

+Writes 16 bytes to the active PICC.
For MIFARE Classic the sector containing the block must be authenticated before calling this function.
For MIFARE Ultralight the operation is called "COMPATIBILITY WRITE".
Even though 16 bytes are transferred to the Ultralight PICC, only the least significant 4 bytes (bytes 0 to 3) are written to the specified address. It is recommended to set the remaining bytes 04h to 0Fh to all logic 0.
return STATUS_OK on success, STATUS_??? otherwise.
byte MFRC522::MIFARE_Write(
byte blockAddr,
| MIFARE Classic: The block (0-0xff) number.
| MIFARE Ultralight: The page (2-15) to write to.
byte *buffer, | The 16 bytes to write to the PICC
byte bufferSize | Buffer size, must be at least 16 bytes. Exactly 16 bytes are
| written.
Example:
byte valueBlockA = 4;
byte value1Block[] = { 1,2,3,4, 5,6,7,8, 9,10,255,12, 13,14,15,16}; status = mfrc522.MIFARE_Write(valueBlockA, value1Block, 16);
if (status != MFRC522::STATUS_OK) {
Serial.print("MIFARE_Write() failed: "); Serial.println(mfrc522.GetStatusCodeName(status));
}

+MIFARE Decrement subtracts the delta from the value of the addressed block, and stores the result in a volatile memory.
For MIFARE Classic only. The sector containing the block must be authenticated before calling this function.
Only for blocks in "value block" mode, ie with access bits [C1 C2 C3] = [110] or [001].
Use MIFARE_Transfer() to store the result in a block.
return STATUS_OK on success, STATUS_??? otherwise.
byte MFRC522::MIFARE_Decrement(
byte blockAddr, | The block (0-0xff) number.
long delta | This number is subtracted from the value of block blockAddr.

+MIFARE Increment adds the delta to the value of the addressed block, and stores the result in a volatile memory.
For MIFARE Classic only. The sector containing the block must be authenticated before calling this function.
Only for blocks in "value block" mode, ie with access bits [C1 C2 C3] = [110] or

[001].
Use MIFARE_Transfer() to store the result in a block. return STATUS_OK on success, STATUS_??? otherwise.
byte MFRC522::MIFARE_Increment(
byte blockAddr, | The block (0-0xff) number.
long delta | This number is added to the value of block blockAddr.
Example:
// Add 1 to the value of valueBlockA and store the result in valueBlockA. byte valueBlockA = 5;
Serial.print("Adding 1 to value of block "); Serial.println(valueBlockA); byte status = mfrc522.MIFARE_Increment(valueBlockA, 1);
if (status != MFRC522::STATUS_OK) {
Serial.print("MIFARE_Increment() failed: "); Serial.println(mfrc522.GetStatusCodeName(status)); return;
}
status = mfrc522.MIFARE_Transfer(valueBlockA);
if (status != MFRC522::STATUS_OK) { Serial.print("MIFARE_Transfer() failed: "); Serial.println(mfrc522.GetStatusCodeName(status)); return;
}

+MIFARE Restore copies the value of the addressed block into a volatile memory.
For MIFARE Classic only. The sector containing the block must be authenticated before calling this function.
Only for blocks in "value block" mode, ie with access bits [C1 C2 C3] = [110] or [001].
Use MIFARE_Transfer() to store the result in a block.
return STATUS_OK on success, STATUS_??? otherwise.
byte MFRC522::MIFARE_Restore(
byte blockAddr The block (0-0xff) number.
The datasheet describes Restore as a two step operation, but does not explain what data to transfer in step 2.Doing only a single step does not work, so I chose to transfer 0L in step two.

+Helper function for the two-step MIFARE Classic protocol operations Decrement, Increment and Restore.
return STATUS_OK on success, STATUS_??? otherwise.
byte MFRC522::MIFARE_TwoStepHelper(
byte command, | The command to use
byte blockAddr, | The block (0-0xff) number.
long data | The data to transfer in step 2
)

+MIFARE Transfer writes the value stored in the volatile memory into one MIFARE Classic block.
For MIFARE Classic only. The sector containing the block must be authenticated before calling this function.
Only for blocks in "value block" mode, ie with access bits [C1 C2 C3] = [110] or [001].
return STATUS_OK on success, STATUS_??? otherwise.
byte MFRC522::MIFARE_Transfer(
byte blockAddr The block (0-0xff) number.

+Returns a string pointer to a status code name. const char *MFRC522::GetStatusCodeName(
byte code | One of the StatusCode enums.
code values | return values

STATUS_OK: | "Success."
STATUS_ERROR: | "Error in communication."
STATUS_COLLISION: | "Collision detected."
STATUS_TIMEOUT: | "Timeout in communication."
STATUS_NO_ROOM: | "A buffer is not big enough."
STATUS_INTERNAL_ERROR: "Internal error in the code. Should not happen."
STATUS_INVALID: | "Invalid argument."
STATUS_CRC_WRONG: | "The CRC_A does not match."
STATUS_MIFARE_NACK: | "A MIFARE PICC responded with NAK."
default: | "Unknown error"

Example:
Serial.println(mfrc522.GetStatusCodeName(status));

+Translates the SAK (Select Acknowledge) to a PICC type. return PICC_Type
byte MFRC522::PICC_GetType(
byte sak | The SAK byte returned from PICC_Select().
sak | return value
sak & 0x04 | PICC_TYPE_NOT_COMPLETE
0x09 | PICC_TYPE_MIFARE_MINI
0x08 | PICC_TYPE_MIFARE_1K
0x18 | PICC_TYPE_MIFARE_4K
0x00 | PICC_TYPE_MIFARE_UL
0x10 or 0x11 | PICC_TYPE_MIFARE_PLUS
0x01 | PICC_TYPE_TNP3XXX
sak & 0x20 | PICC_TYPE_ISO_14443_4
sak & 0x40 | PICC_TYPE_ISO_18092
else | PICC_TYPE_UNKNOWN

+Returns a string pointer to the PICC type name. const char *MFRC522::PICC_GetTypeName(
byte piccType | One of the PICC_Type enums.
piccType | return value
PICC_TYPE_ISO_14443_4 | "PICC compliant with ISO/IEC 14443-4"
PICC_TYPE_ISO_18092: | "PICC compliant with ISO/IEC 18092 (NFC)"
PICC_TYPE_MIFARE_MINI | "MIFARE Mini, 320 bytes"
PICC_TYPE_MIFARE_1K | "MIFARE 1KB"
PICC_TYPE_MIFARE_4K | "MIFARE 4KB"
PICC_TYPE_MIFARE_UL | "MIFARE Ultralight or Ultralight C"
PICC_TYPE_MIFARE_PLUS | "MIFARE Plus"
PICC_TYPE_TNP3XXX | "MIFARE TNP3XXX"
PICC_TYPE_NOT_COMPLETE "SAK indicates UID is not complete."
PICC_TYPE_UNKNOWN | "Unknown type”
Example:
Serial.println(mfrc522.PICC_GetTypeName(piccType));

+Dumps debug info about the selected PICC to Serial.
On success the PICC is halted after dumping the data.
For MIFARE Classic the factory default key of 0xFFFFFFFFFFFF is tried. void MFRC522::PICC_DumpToSerial(
Uid *uid Pointer to Uid struct returned from a successful PICC_Select(). Example:
mfrc522.PICC_DumpToSerial(&(mfrc522.uid));

+Dumps memory contents of a sector of a MIFARE Classic PICC.
Uses PCD_Authenticate(), MIFARE_Read() and PCD_StopCrypto1.

Always uses PICC_CMD_MF_AUTH_KEY_A because only Key A can always read the sector trailer access bits.
void MFRC522::PICC_DumpMifareClassicSectorToSerial(
Uid *uid, | Pointer to Uid struct returned from a successful PICC_Select()
MIFARE_Key *key, Key A for the sector.
byte sector | The sector to dump, 0..39.

+Calculates the bit pattern needed for the specified access bits. In the [C1 C2 C3] tuples C1 is MSB (=4) and C3 is LSB (=1).
void MFRC522::MIFARE_SetAccessBits(
byte *accessBitBuffer, Pointer to byte 6, 7 and 8 in the sector trailer.
| Bytes [0..2] will be set.
byte g0, | Access bits [C1 C2 C3] for block 0 (for sectors 0-31) or blocks 0-4 (for sectors 32-39)
byte g1, | Access bits C1 C2 C3] for block 1 (for sectors 0-31) or blocks 5-9 (for sectors 32-39)
byte g2, | Access bits C1 C2 C3] for block 2 (for sectors 0-31) or blocks 10-14 (for sectors 32-39)
byte g3 | Access bits C1 C2 C3] for the sector trailer, block 3 (for sectors 0-31) or block 15 (for sectors 32-39)

The access bits are stored in a peculiar fashion.
There are four groups:

g[3] Access bits for the sector trailer, block 3 (for sectors 0-31) or block 15 (for sectors 32-39)

g[2] Access bits for block 2 (for sectors 0-31) or blocks 10-14 (for sectors 32-39) g[1] Access bits for block 1 (for sectors 0-31) or blocks 5-9 (for sectors 32-39) g[0] Access bits for block 0 (for sectors 0-31) or blocks 0-4 (for sectors 32-39)

Each group has access bits [C1 C2 C3]. In this code C1 is MSB and C3 is LSB.
The four CX bits are stored together in a nibble cx and an inverted nibble cx_. Example:
// Sector trailer that defines blocks 5 and 6 as Value Blocks and enables key B. byte trailerBuffer[] = {255,255,255,255,255,255,0,0,0,0, 255,255,255,255,255,255}; // Keep default keys.
// g1=6(i.e.110) => block 5 value block. Key B write&increment, A or B decrement. // g2=6 => Same thing for block 6.
// g3=3 => Key B must be used to modify the Sector Trailer. Key B becomes valid. mfrc522.MIFARE_SetAccessBits(&trailerBuffer[6], 0, 6, 6, 3);

+Check if a card is present
bool MFRC522::PICC_IsNewCardPresent()
Returns true if a PICC responds to PICC_CMD_REQA.
Only "new" cards in state IDLE are invited. Sleeping cards in state HALT are ignored. Example:
// Look for new cards
if ( ! mfrc522.PICC_IsNewCardPresent()) return;

+Read Card Serial
bool MFRC522::PICC_ReadCardSerial()
Simple wrapper around PICC_Select.
Returns true if a UID could be read.The read UID is available in the class variable uid.
Remember to call PICC_IsNewCardPresent(), PICC_RequestA() or PICC_WakeupA() first. return true if one selected

Now a card is selected. The UID and SAK is in mfrc522.uid. Example:
Serial.print("Card UID:");
for (byte i = 0; i < mfrc522.uid.size; i++) { Serial.print(mfrc522.uid.uidByte[i] < 0x10 ? " 0" : " "); Serial.print(mfrc522.uid.uidByte[i], HEX);
}
// Dump PICC type
byte piccType = mfrc522.PICC_GetType(mfrc522.uid.sak); Serial.print("PICC type: "); Serial.println(mfrc522.PICC_GetTypeName(piccType));
if ( piccType != MFRC522::PICC_TYPE_MIFARE_MINI
&& piccType != MFRC522::PICC_TYPE_MIFARE_1K
&& | piccType != MFRC522::PICC_TYPE_MIFARE_4K) {
Serial.println("This sample only works with MIFARE Classic cards."); return;
}

How to convert a normal block into a value block
Usually a normal block has 000 access bits, while a value block has 110 access bits Example:
byte valueBlockA = 5;
byte valueBlockB = 6;
byte trailerBlock = 7;
// We need a sector trailer with blocks 5 and 6 as Value Blocks and enables key B. byte trailerBuffer[] = { 255,255,255,255,255,255,
| 0,0,0,0,255,255,255,255,255,255}; // Keep default keys.
// g1=6 => block 5 as value block. Key B to write&increment, A or B for decrement. // g2=6 => Same thing for block 6.
// g3=3 => Key B must be used to modify the Sector Trailer. Key B becomes valid. mfrc522.MIFARE_SetAccessBits(&trailerBuffer[6], 0, 6, 6, 3);
byte status = mfrc522.MIFARE_Write(trailerBlock, trailerBuffer, 16);
if (status != MFRC522::STATUS_OK) {
Serial.print("MIFARE_Write() failed: "); Serial.println(mfrc522.GetStatusCodeName(status));
return;
}

How to setup a Value Block with a value set to zero Example:
byte blockAddr=5;
byte valueBlock[] = {0,0,0,0, 255,255,255,255, 0,0,0,0,
| blockAddr,~blockAddr,blockAddr,~blockAddr };
byte status = mfrc522.MIFARE_Write(blockAddr, valueBlock, 16); if (status != MFRC522::STATUS_OK) { Serial.print("MIFARE_Write() failed: "); Serial.println(mfrc522.GetStatusCodeName(status));
}

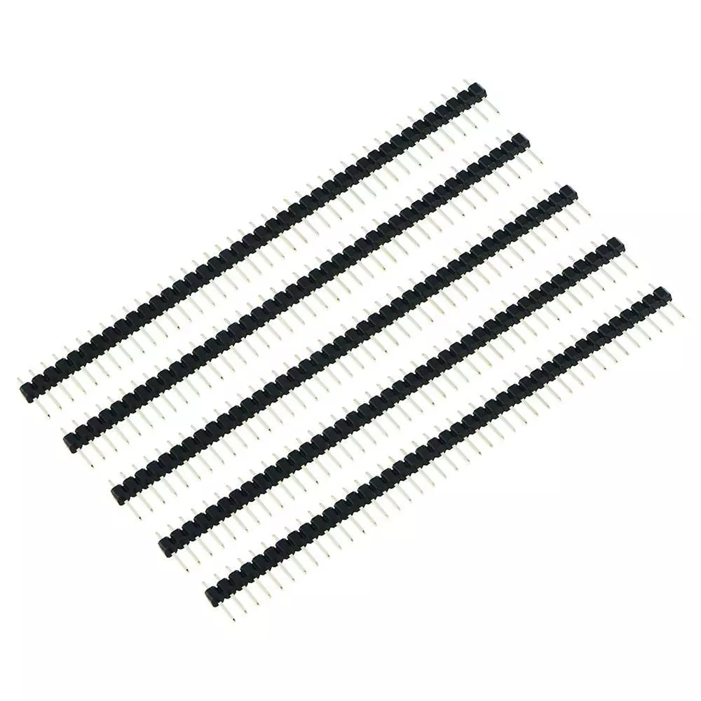
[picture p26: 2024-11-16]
images/docs_03/BrochesMales.webp

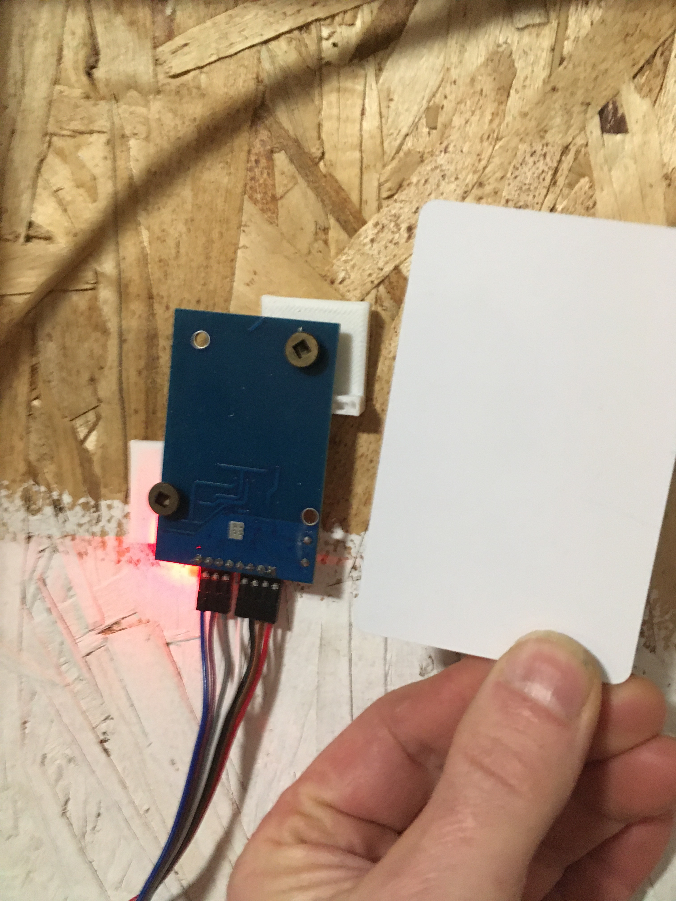
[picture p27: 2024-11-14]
images/CarteEtLecteur.jpg

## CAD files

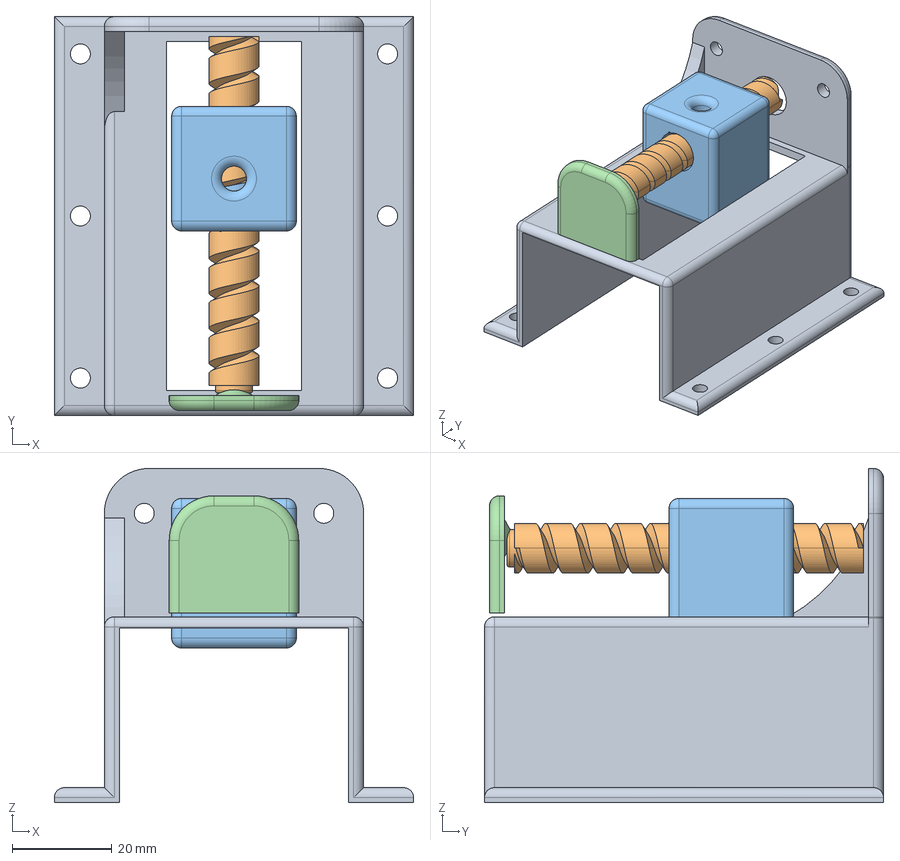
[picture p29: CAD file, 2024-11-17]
imprime_3d/FreeCad/Motorisation_Barrure_v3.FCStd
72.0 x 80.0 x 67.0 mm
Structure
Boulon
Curseur
Butoir

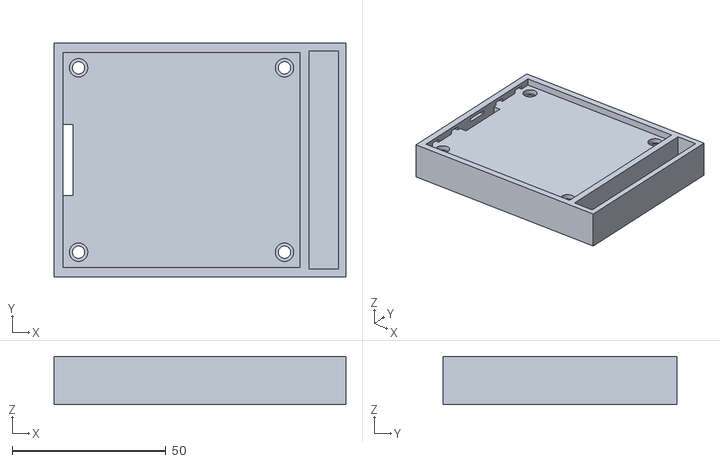
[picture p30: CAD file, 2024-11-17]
imprime_3d/stl/Obudowa.stl
95.0 x 76.0 x 15.6

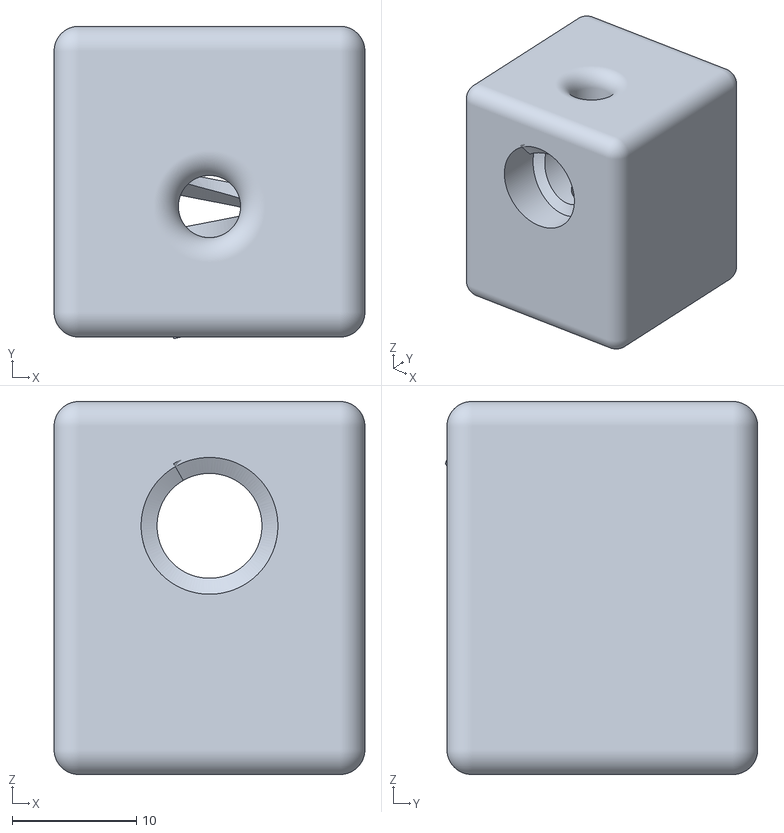
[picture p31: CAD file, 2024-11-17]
imprime_3d/stl/Motorisation_Barrure_v3-Curseur.stl
25.0 x 25.1 x 30.0

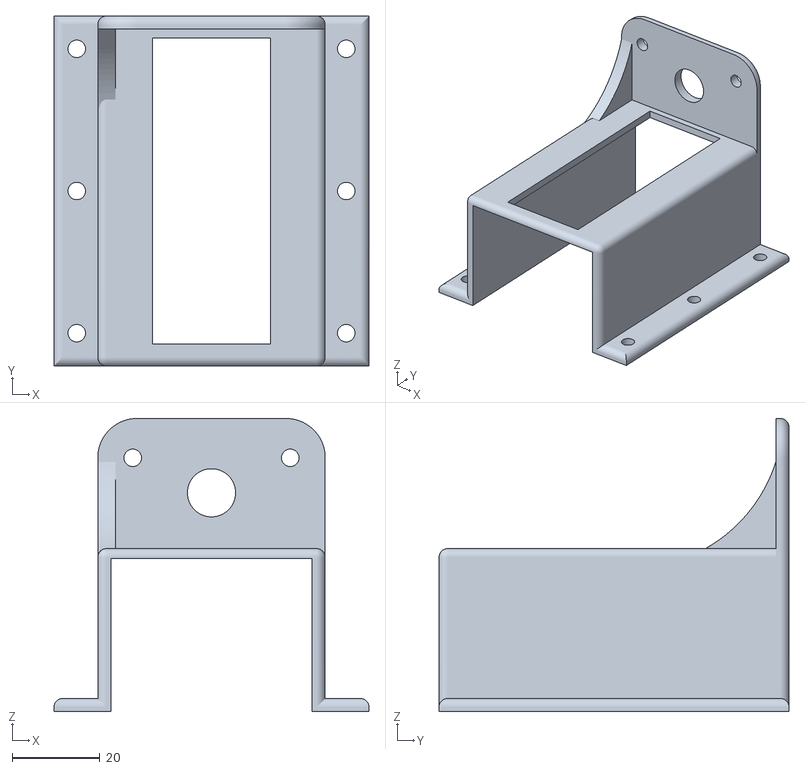
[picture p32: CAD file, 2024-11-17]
imprime_3d/stl/Motorisation_Barrure_v3-Structure.stl
72.0 x 80.0 x 67.0

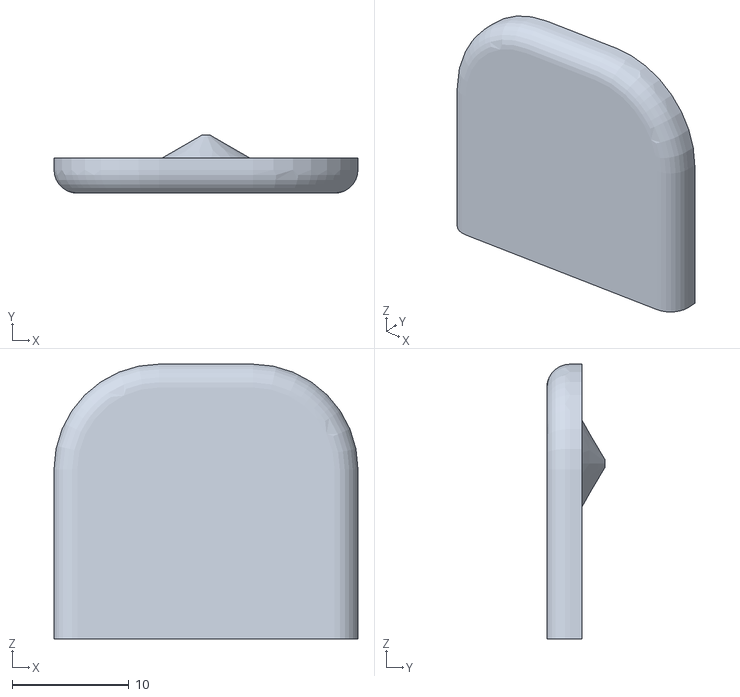
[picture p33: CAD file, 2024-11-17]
imprime_3d/stl/Motorisation_Barrure_v3-Butoir.stl
26.0 x 5.00 x 23.5

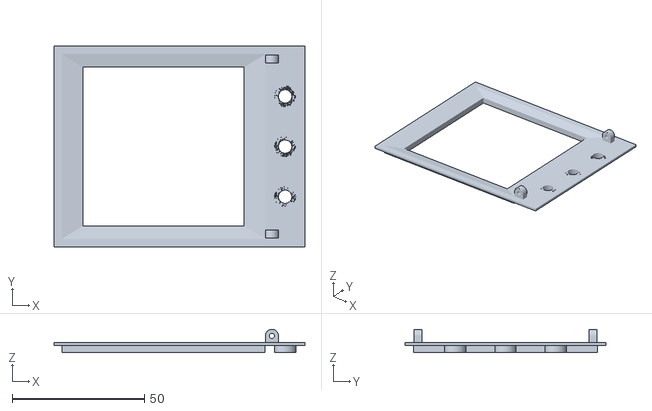
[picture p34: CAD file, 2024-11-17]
imprime_3d/stl/Panel.stl
95.0 x 76.0 x 8.86

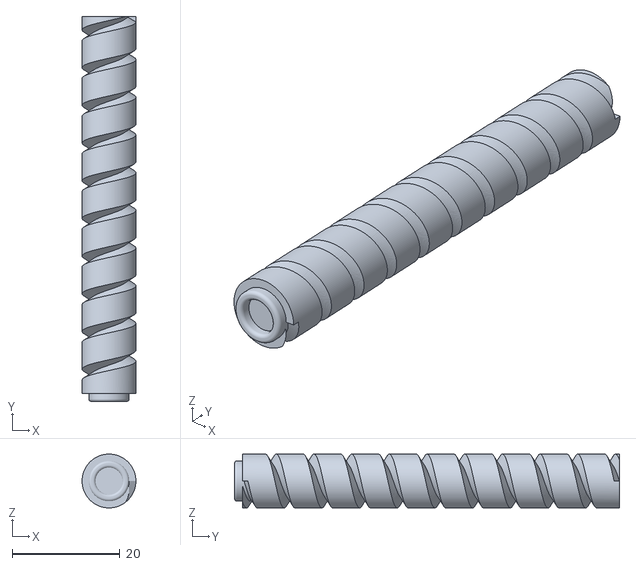
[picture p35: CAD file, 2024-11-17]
imprime_3d/stl/Motorisation_Barrure_v3-Boulon.stl
10.0 x 71.5 x 10.00

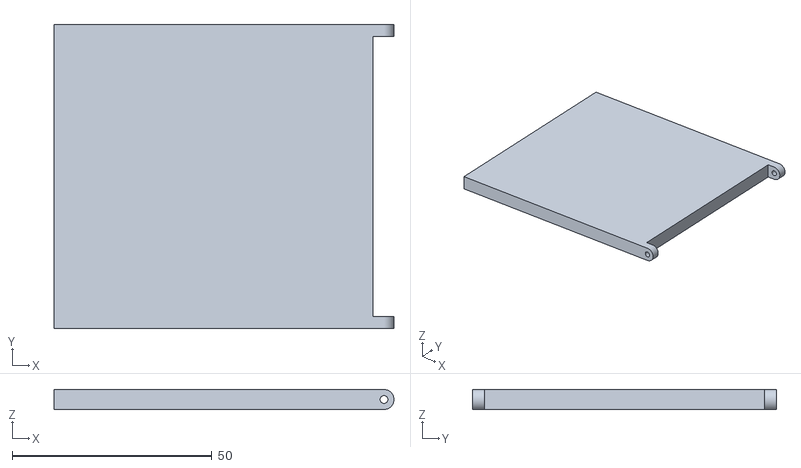
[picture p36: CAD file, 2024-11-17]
imprime_3d/stl/klapka.stl
85.0 x 76.0 x 5.00

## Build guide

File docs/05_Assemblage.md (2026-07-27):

# 5. L'assemblage
---

Une carte spécialisée peut vous accommoder.

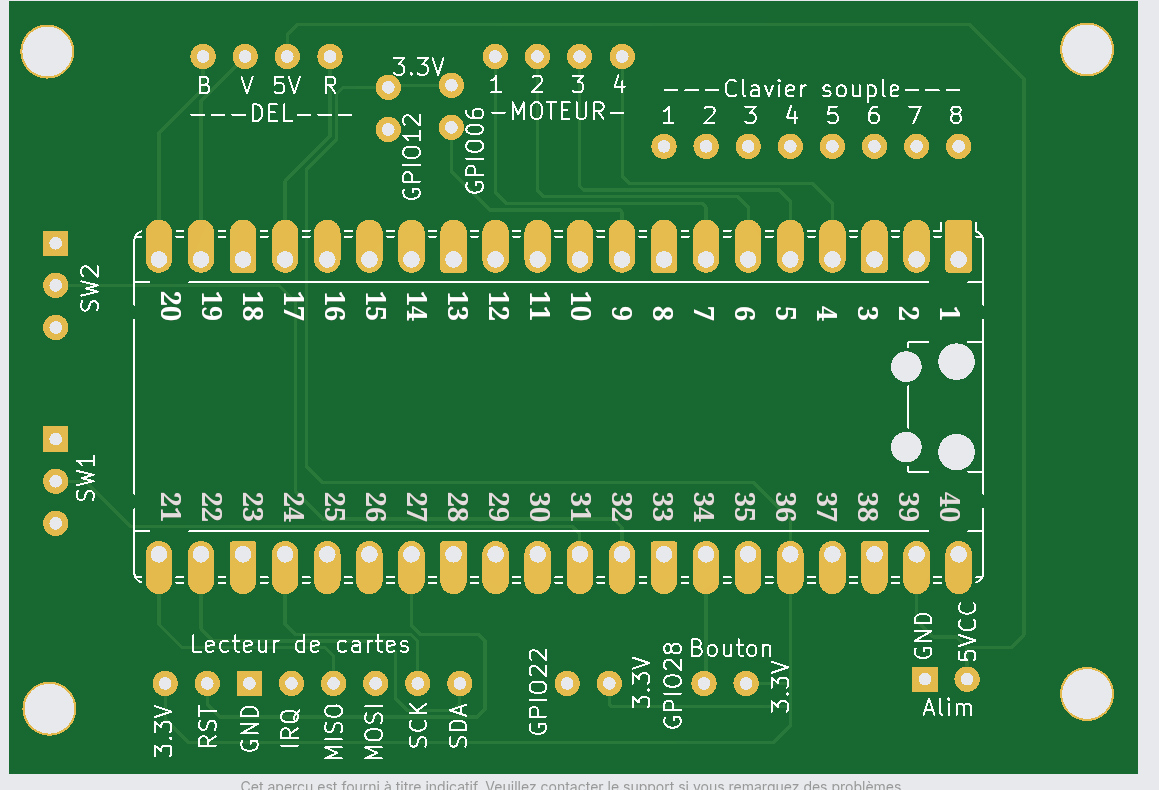
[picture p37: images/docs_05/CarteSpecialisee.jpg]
Carte spécialisée disponible, écrivez-moi


Je l'ai créée pour mes besoins, mais j'ai quelques copies disponibles.  Écrivez-moi à foi02@cartefoi.net

La numérotation des broches de Rasp Pico est importante.  Lorsque vous regardez le micro-contrôleur en le plaçant verticalement, le connecteur USB vers le haut, les numéros vont comme suit.
La broche 1 est en haut à gauche.  En descendant sur le côté gauche, vous aurez ainsi les broches 1 à 20.
Puis, en remontant sur la droite, vous aurez les broches 21 à 40; la broche 40 étant l'alimentation 5 VCC du module et la 39 la mise à terre principale.
Normalement, les numéros 1, 2 et 39 sont imprimés sur la carte, comme le montre l'image suivante.
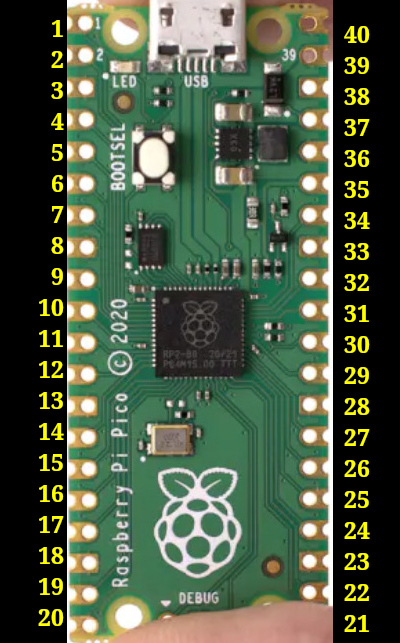
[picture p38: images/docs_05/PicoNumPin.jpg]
Numérotation


## Description des broches de RaspPi, selon l'utilité de ce projet.
Voir toutes les utilités possibles de RaspPico en [cliquant ici](https://pico.pinout.xyz/)

<table>
<tr><td>Broche 1</td><td>  GPIO-00 </td><td>  clavier 4x4 -> 8</td><td> fil blanc-brun</td></tr>
<tr><td>Broche 2</td><td>  GPIO-01 </td><td>  clavier 4x4 -> 7</td><td> fil brun</td></tr>
<tr><td>Broche 3</td><td>  GND</td><td></td><td></td></tr>
<tr><td>Broche 4</td><td>  GPIO-02 </td><td>  Moteur -> 4</td><td> fil blanc-orange</td></tr>
<tr><td>Broche 5</td><td>  GPIO-03 </td><td>  Moteur -> 3</td><td> fil blanc-bleu</td></tr>
<tr><td>Broche 6</td><td>  GPIO-04 </td><td>  Moteur -> 2</td><td> fil blanc-vert</td></tr>
<tr><td>Broche 7</td><td>  GPIO-05 </td><td>  Moteur -> 1</td><td> fil blanc-brun</td></tr>
<tr><td>Broche 8</td><td>  GND</td><td></td><td></td></tr>
<tr><td>Broche 9</td><td>  GPIO-06</td><td></td><td></td></tr>
<tr><td>Broche 10</td><td>  GPIO-07 </td><td>   clavier 4x4 -> 6</td><td>fil blanc-orange</td></tr>
<tr><td>Broche 11</td><td>  GPIO-08 </td><td>   clavier 4x4 -> 5</td><td>fil orange</td></tr>
<tr><td>Broche 12</td><td>  GPIO-09 </td><td>   clavier 4x4 -> 4</td><td>fil blanc-bleu</td></tr>
<tr><td>Broche 13</td><td>  GND</td><td></td><td></td></tr>
<tr><td>Broche 14</td><td>  GPIO-10 </td><td>   clavier 4x4 -> 3</td><td>fil bleu</td></tr>
<tr><td>Broche 15</td><td>  GPIO-11 </td><td>   clavier 4x4 -> 2</td><td>fil blanc-vert</td></tr>
<tr><td>Broche 16</td><td>  GPIO-12</td><td></td><td></td></tr>
<tr><td>Broche 17</td><td>  GPIO-13 </td><td>  DEL tricolor -> rouge</td><td>fil orange</td></tr>
<tr><td>Broche 18</td><td>  GND</td><td></td><td></td></tr>
<tr><td>Broche 19</td><td>  GPIO-14 </td><td>  DEL tricolor -> vert</td><td>fil vert</td></tr>
<tr><td>Broche 20</td><td>  GPIO-15 </td><td>  DEL tricolor -> bleu</td><td>fil bleu</td></tr>
<tr><td>Broche 21</td><td>  SPI -> RX </td><td>  Carte identification -> MISO  </td><td> fil blanc-vert</td></tr>
<tr><td>Broche 22</td><td>  SPI -> CS </td><td>  Carte identification -> SDA  </td><td> fil blanc-bleu</td></tr>
<tr><td>Broche 23</td><td>  GND</td><td></td><td></td></tr>
<tr><td>Broche 24</td><td>  SPI -> CLK </td><td>  Carte identification -> SCK  </td><td> fil blanc-brun</td></tr>
<tr><td>Broche 25</td><td>  SPI -> TX </td><td>  Carte identification -> MOSI  </td><td> fil bleu</td></tr>
<tr><td>Broche 26</td><td>  GPIO-20 </td><td>  clavier 4x4 -> 1</td><td> vert</td></tr>
<tr><td>Broche 27</td><td>  GPIO-21 </td><td>  Carte identification -> RST </td><td> fil vert</td></tr>
<tr><td>Broche 28</td><td>  GND</td><td></td><td></td></tr>
<tr><td>Broche 29</td><td>  GPIO-22 </td><td>  Bouton d'activation de la barrure, côté maison</td><td>fil bleu</td></tr>
<tr><td>Broche 30</td><td>  GPIO-26 </td><td>  Interrupteur fermé lorsque la porte est fermée -> SGN</td><td>fil blanc-vert</td></tr>
<tr><td>Broche 31</td><td>  GPIO-27 </td><td>  Interrupteur fermé lorsque la porte est ouverte -> SGN</td><td>fil vert</td></tr>
<tr><td>Broche 32</td><td>  GND</td><td></td><td></td></tr>
<tr><td>Broche 33</td><td>  ADC GND</td><td></td><td></td></tr>
<tr><td>Broche 34</td><td>  GPIO-28</td><td></td><td></td></tr>
<tr><td>Broche 35</td><td>  ADC Vref</td><td></td><td></td></tr>
<tr><td>Broche 36</td><td>  3.3 VCC out </td><td>  Alimentation de divers composants en 3.3 volts</td><td>fils oranges</td></tr>
<tr><td>Broche 37</td><td>  3.3 V en</td><td></td><td></td></tr>
<tr><td>Broche 38</td><td>  GND </td><td>  Mise à terre</td><td>fils bruns</td></tr>
<tr><td>Broche 39</td><td>  5VCC </td><td>  Alimentation du Rasp Pico</td><td>fil rouge</td></tr>
<tr><td>Broche 40</td><td>  Vbus 5V</td><td></td><td></td></tr>
</table>

[Câblage](04_Cablage.md)  <<<  [Table des matières](README.md)   >>>    [Impression 3d](06_Impression_3d.md)

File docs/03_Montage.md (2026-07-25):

# 3a. Le montage du circuit

## Le Raspberry PI pico sur une carte
Puisque vous serez appelé(e) à programmer ou corriger le programme à quelques reprises afin de répondre à vos besoin, je vous suggère de NE PAS souder le Raspberry PI Pico (ci-bas nommé Pico) directement sur la carte perforée.  Optez plutôt pour des broches mâles sur le Pico et des réceptacles femelles sur la carte perforée.

Si vous souhaitez limiter la consommation de broches et de matériel en général, vous pouvez limiter vos soudures aux seuls éléments utilisés.
<br clear="all" />
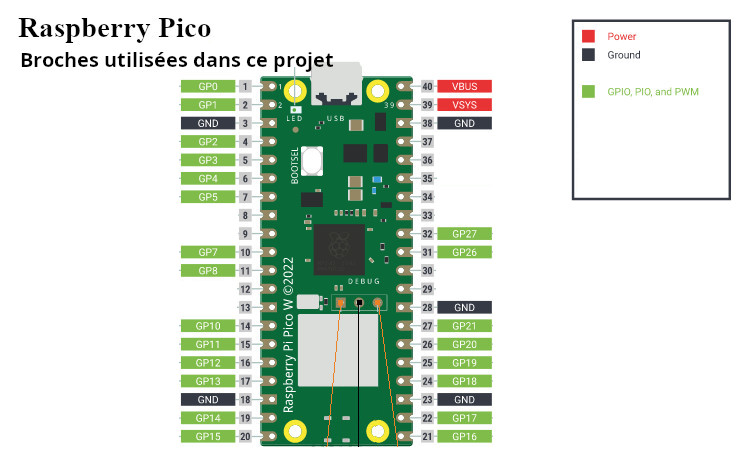
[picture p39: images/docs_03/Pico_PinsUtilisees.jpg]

<br clear="all" />
<table width="100%">
	<tr><td colspan="5">Soudez les broches mâles sur le Raspberry PI Pico</td></tr>
	<tr>
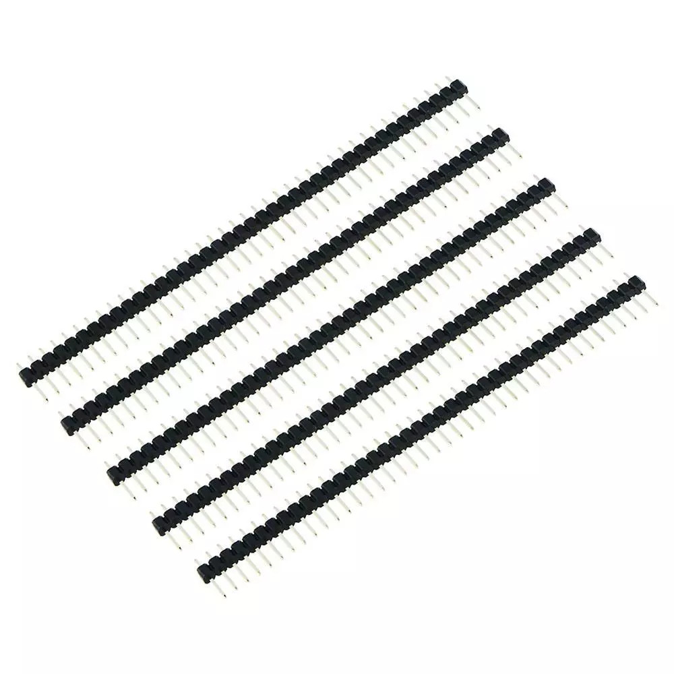
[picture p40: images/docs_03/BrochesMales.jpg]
		<td></td>
		<td></td>
		<td>Image d`internet: Rasp PI pico</td>
		<td></td>
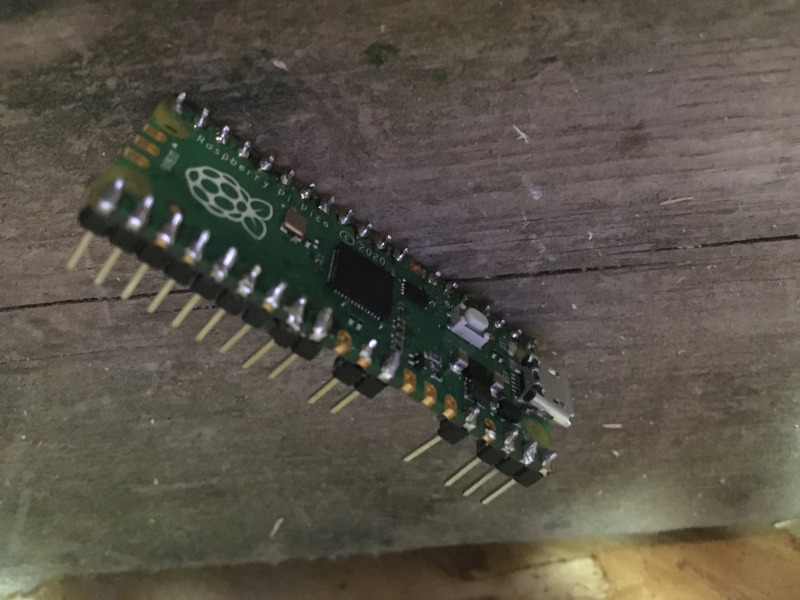
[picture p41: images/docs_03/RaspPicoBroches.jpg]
Raspberry avec broches
		<td></td>
	</tr>
	<tr><td colspan="5">Soudez les broches femelles sur la carte perforée.</td></tr>
	<tr>
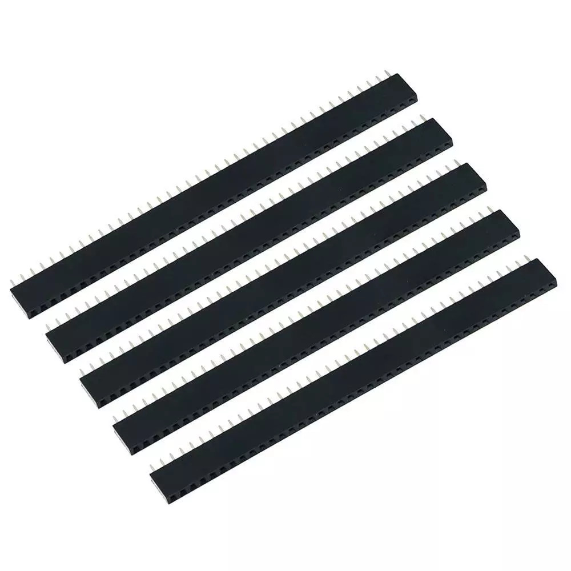
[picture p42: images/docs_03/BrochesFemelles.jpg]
		<td></td>
		<td></td>
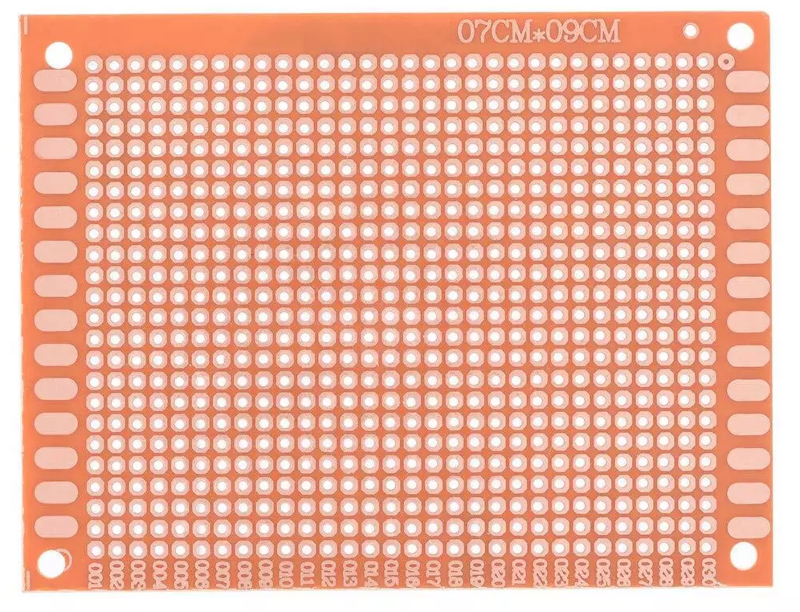
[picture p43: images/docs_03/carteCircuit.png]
Image d`internet: Rasp PI pico
		<td></td>
		<td></td>
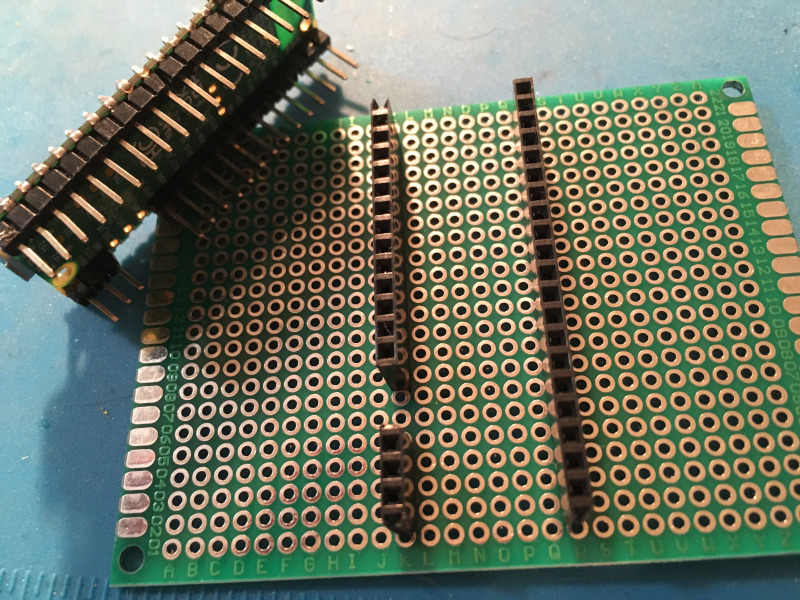
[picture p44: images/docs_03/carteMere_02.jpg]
Carte mère
		<td></td>
	</tr>
</table>

Voici comment seront utilisées les broches du Pico dans notre projet.
<br clear="all" />
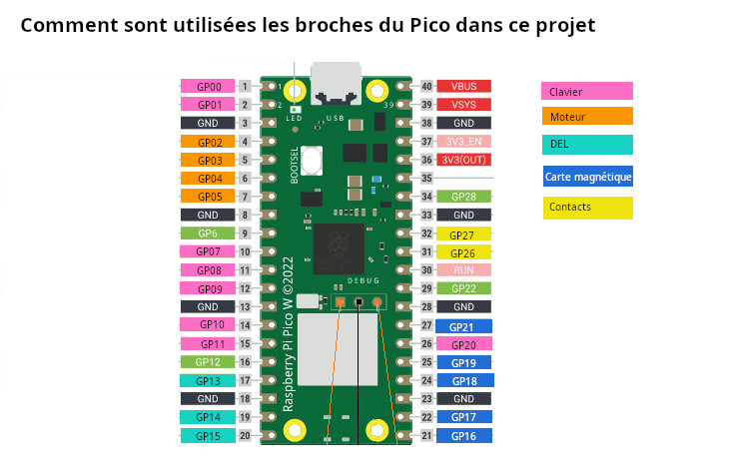
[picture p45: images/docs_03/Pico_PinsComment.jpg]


# 3b. Le montage mécanique
À ce point, il serait bon de considérer l'installation du verrou sur votre porte.
Assurez-vous qu'il coulisse librement et facilement, que le verouillage se fasse sans effort de même que le déverrouillage.
Gardez en tête que le petit moteur développe peu de puissance, que le tout est assemblé avec du plastique imprimé et  - donc - que toutes les composantes sont fragiles.
Le mouvement du verrou doit donc en tous points être facile et fluide.

Les principaux points à vérifier:
* insértion (et retrait) du verrou dans le logement de fermeture: alignement parfait, aisance de mouvement.
[Voyez en action - fichier MP4](../images/videos/deverrouillage.mp4)

* le tenon du verrou ne doit pas s'engager dans les fentes d'immobilisation.

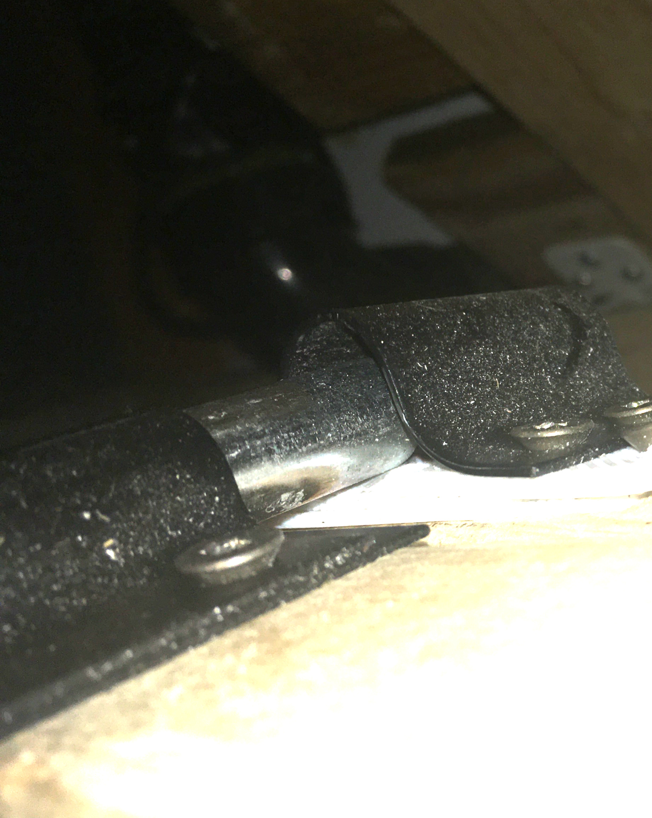
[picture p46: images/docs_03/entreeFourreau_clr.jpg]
tenon en fourreau

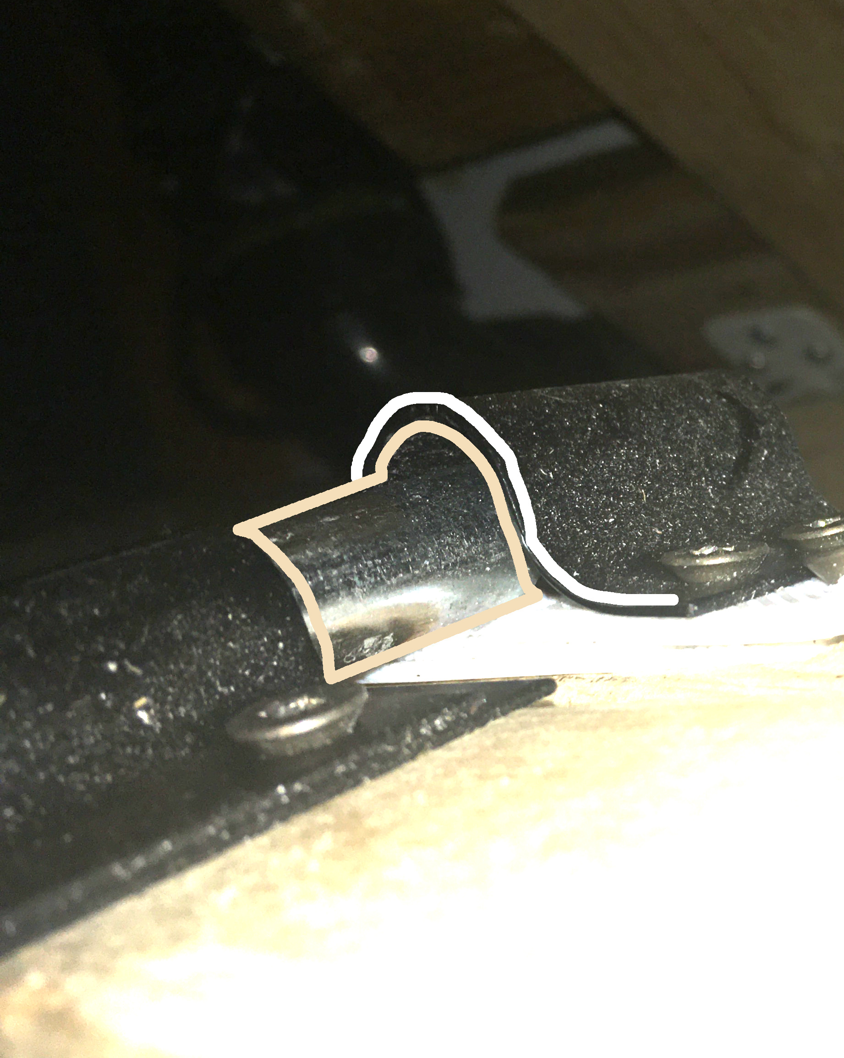
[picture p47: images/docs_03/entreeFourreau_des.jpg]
tenon en fourreau

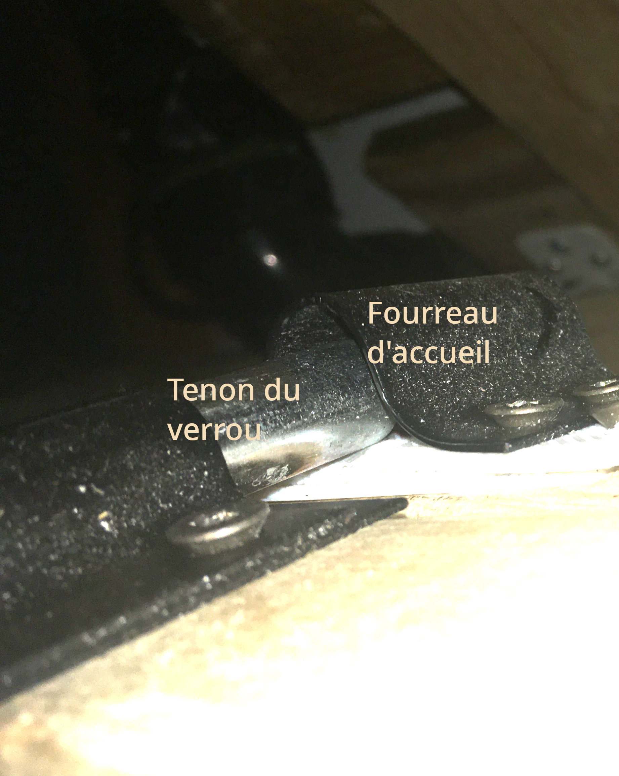
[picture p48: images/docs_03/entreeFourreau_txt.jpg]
tenon en fourreau

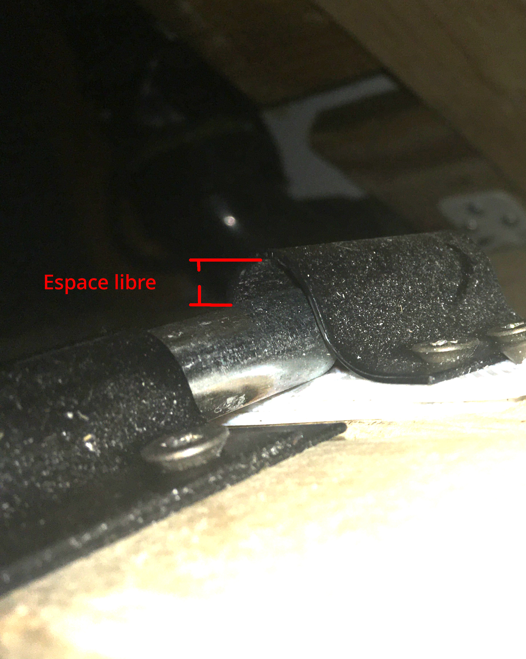
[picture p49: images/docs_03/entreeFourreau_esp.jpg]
tenon en fourreau


---

[Le nécessaire](02_MaterielNecessaire.md)  <<<  [Table des matières](README.md)   >>>    [Le câblage](04_Cablage.md)

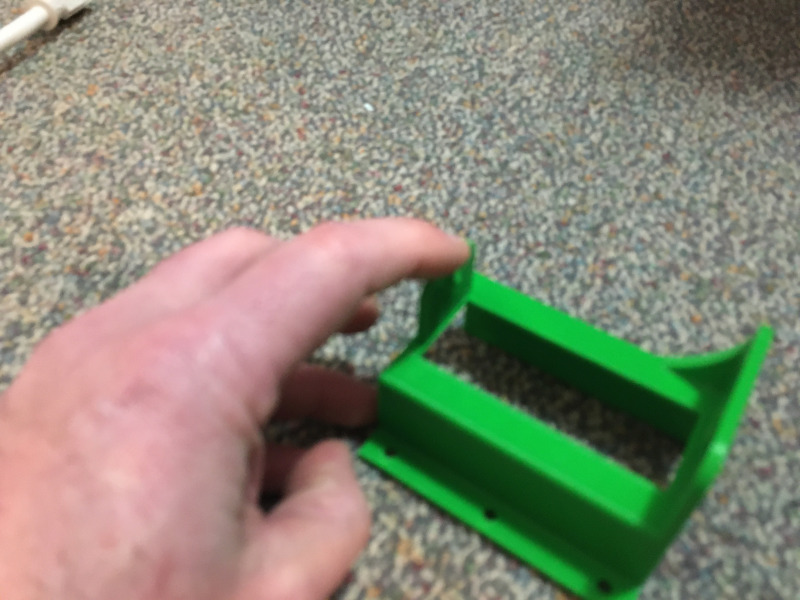
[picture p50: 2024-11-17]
images/impression3d/butoir_Assembler.jpg

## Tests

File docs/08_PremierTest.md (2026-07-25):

# 8. Vos premiers test et les ajustements initiaux

## Assemblage initial et premier test
Le premier test vise à vérifier la réponse des différents composants électroniques et de la programmation

Nous nous ne réalisons ici que les connexions électriques et procédons à un test à vide.
Les pièces suivantes devraient être connectées:
* Les deux interrupteurs de limites aux bornes leur correspondant sur RaspPi
* Le moteur à son alimentation électrique
* Le moteur à sa carte de contrôle
* La carte de contrôle au RaspPi
* Le lecteur de carte magnétique à l'alimentation et au RaspPi
* Les quatres broches de la DEL aux bornes leur correspondant sur RaspPi
* Le RaspPi à son alimentation électrique

Idéalement, suivez l'évolution de ce test en gardant le RaspPi connecté à votre ordinateur et en affichant le terminal sur votre Arduino IDE

1. Alimentez le système.
2. La DEL devrait s'allumer et clignoter pendant que des messages apparaîtront sur l'Arduino IDE témoignant des étapes de mise en marche
3. Le moteur se mettra en marche et ne cessera de fonctionner qu'au moment où vous appuyerez sur le commutateur de distance « ouvert »

## Test avec verrou
Avant de procéder à ce deuxième test, assurez-vous que la barre du verrou se déplace librement et facilement dans son fourreau, qu'il entre sans effort dans le loquet.

## Ajustements

## Fixation définitive des interrupteurs
---
[La programmation](07_Programmation.md)  <<<  [Table des matières](README.md)   >>>  [Félicitations!](09_Felicitations.md)

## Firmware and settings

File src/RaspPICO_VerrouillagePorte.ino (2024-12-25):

#include <Stepper.h>
#include <SPI.h>
#include <MFRC522.h>
#include <Keypad.h>

//Raspberry Pi Pico (non, pas Wifi)
//----------------------------Liste des GPIO attribués au projet ci-bas ---------------------------------------------------------------------
//00  clavier 4x4 - blanc-brun
//01	clavier 4x4 - brun
//02	Moteur - blanc-orange
//03	Moteur - blanc-bleu
//04	Moteur - blanc-vert
//05	Moteur - blanc-brun
//06	
//07	clavier 4x4 - blanc-orange
//08	clavier 4x4 - orange
//09	clavier 4x4 - blanc-bleu
//10	clavier 4x4 - bleu
//11	clavier 4x4 - blanc-vert
//12	
//13	pinDER - rouge
//14	pinDEV - vert
//15	pinDEB - bleu
//16	Carte identification    -- blanc-vert
//17	Carte identification    -- blanc-bleu
//18	Carte identification    -- blanc-brun
//19	Carte identification    -- bleu
//20	clavier 4x4 - vert
//21	Carte identification    -- vert
//22	
//26	pinSW1 - Interrupteur fermé lorsque la porte est ouverte
//27	pinSW2 - Interrupteur fermé lorsque la porte est fermée
//28	
//29	
//----------------------------Fin de la liste des GPI0 attribués au projet ci-bas ----------------------------------------------------------

//En vue de fonctionner sous Respberry PICO
/*----- Variables, Pins -----*/
//#define STEPS  4      // Number of steps per revolution of Internal shaft
int delai = 60000;      //La DEL restera allumée - en rouge ou vert - pendant une minute après la fin du mouvement, tandis que durant le mouvement elle affichera jaune
int pas = 20;           // 1 tour = 2048   // Était à 25, ce 12 novembre 2024 à 12h
int sens = 1;
int vitesseMax = 700;      //Max 700
String libre = "oui";
bool tourne = false;
bool initOUV = false;
bool initFER = false;
int rendu = 0;

int pinSW1 = 26;    //GPIO00 = pin 31  -> Interrupteur fermé lorsque la porte est ouverte  => DEL vert
int pinSW2 = 27;    //GPIO01 = pin 32  -> Interrupteur fermé lorsque la porte est fermée   => DEL rouge
int pinMO1 = 2;     //GPIOO2 = pin 4  -> Mouvement du moteur, contrôleur 1
int pinMO2 = 3;     //GPIOO3 = pin 5  -> Mouvement du moteur, contrôleur 2
int pinMO3 = 4;     //GPIOO4 = pin 6  -> Mouvement du moteur, contrôleur 3
int pinMO4 = 5;     //GPIOO5 = pin 7  -> Mouvement du moteur, contrôleur 4
int pinDER = 13;    //GPIO13 = pin 17 -> Rouge de la DEL;    ... DEL tri-colore : ici Rouge
int pinDEV = 14;    //GPIO14 = pin 19 -> Vert de la DEL;     ... DEL tri-colore : ici Vert
int pinDEB = 15;    //GPIO15 = pin 20 -> Bleu de la DEL;     ... DEL tri-colore : ici Bleu
int pinCLA1 = 7;    //GPIO07 = pin 10 -> Clavier 4x4
int pinCLA2 = 8;    //GPIO08 = pin 11 -> Clavier 4x4
int pinCLA3 = 9;    //GPIO09 = pin 12 -> Clavier 4x4
int pinCLA4 = 10;   //GPIO010 =pin 14 -> Clavier 4x4
int pinCLA5 = 11;   //GPIO011 =pin 15 -> Clavier 4x4
int pinCLA6 = 20;   //GPIO020 =pin 26 -> Clavier 4x4
int pinCLA7 = 0;    //GPIO00 = pin 1  -> Clavier 4x4
int pinCLA8 = 1;    //GPIO01 = pin 2  -> Clavier 4x4
byte CRT_RST = 21;  //GPIO21 = pin 27 -> Lecteur de cartes sans contact - Reset
byte CRT_SSC = 17;  //GPIO17 = pin 22 -> Lecteur de cartes sans contact - SS
String codeEntree = "";
String codeValide = "B6580";
const int col = 4;
const int lgn = 4;
String TchClavier[lgn][col] = {
  {"*","0","#","D"},
  {"7","8","9","C"},
  {"4","5","6","B"},
  {"1","2","3","A"}
};
byte pinLgnCLA[lgn] = {7,8,9,10};
byte pinColCLA[col] = {11,20,0,1};
Keypad clavier = Keypad(makeKeymap(TchClavier), pinLgnCLA, pinColCLA, lgn, col);


unsigned long dernBoutonClavier = millis();

//Création des principaux objets
Stepper moteur(32, pinMO1, pinMO3, pinMO2, pinMO4);
/*
Voici comment connecter le module moteur
PINcarte Defn    PICO    GPIO
A1       GND     >>>>>>  >>>>>>>>   AliM GND  - brun
A2       5V      >>>>>>  >>>>>>>>   Alim 5V   - orange
B1       IN1     4       GPIO2                - blanc-orange
B2       IN2     5       GPIO3                - blanc-bleu
B3       IN3     6       GPIO4                - blanc-vert
B4       IN4     7       GPIO5                - blanc-brun
*/
MFRC522 cartes;   // Create MFRC522 instance.
/*
Voici comment connecter les fils du lecteur de cartes magnétiques, les coueleurs sont celles de la porte secrète de Pond Inlet
PINcarte Defn    PICO    GPIO                                   Couleur
1       3.3V     >>>>>>  >>>>>>>>>>   Alim 3.3 volts            Bleu
2       RST      27      GPIO21                                 Bourgogne
3       GND      >>>>>>  >>>>>>>>>>   Alim GND                  Gris
4       RQ       >>>>>>  >>>>>>>>>>   Libre (non-connecté)
5       MISO     21      GPIO16                                 Blanc
6       MOSI     25      GPIO19                                 Noir
7       SCK      24      GPIO18                                 Brun
8       SDA      22      GPIO17                                 Rouge
*/

void setup() { 
  Serial.begin(115200);
  Serial.println("");
  delay(550);
  Serial.println("Bonjour les testeurs");
  SPI.begin();        // Init SPI bus
  Serial.println("SPI est démarré.");
  cartes.PCD_Init(CRT_SSC, CRT_RST); // Init each MFRC522 card
  cartes.PCD_DumpVersionToSerial();

  pinMode(pinSW1, INPUT);   //Interrupteur fermé lorsque la porte est ouverte  => DEL vert
  pinMode(pinSW2, INPUT);   //Interrupteur fermé lorsque la porte est fermée   => DEL rouge
  pinMode(pinMO1, OUTPUT);  //Moteur 1
  pinMode(pinMO2, OUTPUT);  //Moteur 2
  pinMode(pinMO3, OUTPUT);  //Moteur 3
  pinMode(pinMO4, OUTPUT);  //Moteur 4
  pinMode(pinDER, OUTPUT);  //rouge de la DEL
  pinMode(pinDEV, OUTPUT);  //vert de la DEL
  pinMode(pinDEB, OUTPUT);  //bleu de la DEL

  digitalWrite(pinMO1, LOW);
  digitalWrite(pinMO2, LOW);
  digitalWrite(pinMO3, LOW);
  digitalWrite(pinMO4, LOW);
  digitalWrite(pinDER, LOW);
  digitalWrite(pinDEV, LOW);
  digitalWrite(pinDEB, LOW);

  delay(1000);

  if (digitalRead(pinSW1) == digitalRead(pinSW2)) {
    Serial.println("Nous avons trouvé le verrou en position médiane; nous ouvrons la porte.");
    libre = "ouvrons";
    mouvonsMoteur();
  }
  Serial.println("Voici que tout est défini.  Il ne reste qu`à jouer de la porte.");

}  // fin de setup()

void loop() {
  if (++rendu > 100) { rendu = 0; Serial.println("Nous voici en début de boucle."); }
  if (millis()-dernBoutonClavier < 5000) {
    digitalWrite(pinDER, LOW);
    digitalWrite(pinDEV, LOW);
    digitalWrite(pinDEB, HIGH);
  } else {
    codeEntree = "";
    digitalWrite(pinDER, LOW);
    digitalWrite(pinDEV, LOW);
    digitalWrite(pinDEB, LOW);
  }
  char touche = clavier.getKey();
  if ( (!cartes.PICC_IsNewCardPresent() || !cartes.PICC_ReadCardSerial()) && touche == NO_KEY && rien() ) {
    delay(50);
    return;
  }
  digitalWrite(pinDER, LOW);
  digitalWrite(pinDEV, LOW);
  digitalWrite(pinDEB, HIGH);
  if (carteValide(cartes.uid.uidByte, cartes.uid.size)) { 
    Serial.println("La carte a été jugée valide.");
    libre = "ouvrons";
    sens = 1;
  } else { 
    //Serial.println("Mauvause carte"); 
    libre = "oui"; 
  }
  if (touche != NO_KEY) {
    if (rien()) { return; }
      Serial.print  ("  1: ");
      Serial.print  (digitalRead(pinCLA1));
      Serial.print  ("  2: ");
      Serial.print  (digitalRead(pinCLA2));
      Serial.print  ("  3: ");
      Serial.print  (digitalRead(pinCLA3));
      Serial.print  ("  4: ");
      Serial.print  (digitalRead(pinCLA4));
      Serial.print  ("  5: ");
      Serial.print  (digitalRead(pinCLA5));
      Serial.print  ("  6: ");
      Serial.print  (digitalRead(pinCLA6));
      Serial.print  ("  7: ");
      Serial.print  (digitalRead(pinCLA7));
      Serial.print  ("  8: ");
      Serial.println(digitalRead(pinCLA8));
    if (libre != "oui") { return; }
    Serial.println("Entrons ici dans les tests de clavier");
    if (String(touche) == "*") { 
      //Demande de fermeture
      sens = -1;
      libre = "fermons";
    } else if (String(touche) == "#") {
      //Testons validité du code
      if (codeEntree == codeValide ) { 
        libre = "ouvrons";
        sens = 1;
        Serial.print  ("Accès via code valide : ");
        Serial.println("codeEntree");
      } else {
        digitalWrite(pinDEV, LOW);
        digitalWrite(pinDEB, LOW);
        for (int x=0; x<3; x++) { digitalWrite(pinDER, HIGH); delay(100); digitalWrite(pinDER, LOW);  delay(50); }
        for (int x=0; x<5; x++) { digitalWrite(pinDER, HIGH); delay(30);  digitalWrite(pinDER, LOW);  delay(25); }
        codeEntree = ""; 
        return; 
      }
    } else {
      codeEntree = codeEntree + String(touche);
      digitalWrite(pinDER, LOW);
      digitalWrite(pinDEV, LOW);
      digitalWrite(pinDEB, HIGH);
      dernBoutonClavier = millis();
      return;
    }
    Serial.println("Fin des tests de clavier");
  }

  if (libre != "fermons" && libre != "ouvrons") { return; }
  Serial.println("Activons les mouvements du moteur");
  if (digitalRead(pinSW2) == LOW) {
    sens = -1;
    libre = "fermons";
  }

  digitalWrite(pinDER, LOW);
  for (int x=0; x<5; x++) {
      digitalWrite(pinDEB, HIGH);
      delay(200);
      digitalWrite(pinDEV, LOW);
      digitalWrite(pinDEB, LOW);
      delay(50);
  }
  Serial.println("Fin du signal lumineux confirmant la lecteur réussie.  On passe au jaune.");
  mouvonsMoteur();
} //Fin de loop()

void mouvonsMoteur() {
  Serial.print  ("État de la situation: ");
  Serial.println(libre);

  digitalWrite(pinDER, HIGH);
  digitalWrite(pinDEV, HIGH);
  digitalWrite(pinDEB, LOW);
    Serial.print  ("Vitesse du moteur: ");
    Serial.println(vitesseMax);
    Serial.print  ("Pas du moteur: ");
    Serial.println(pas);
  int tours = 1;
  int vitesse = 100;
  
  //Mouvement
  while (libre == "ouvrons" || libre == "fermons") {
    if (tours/2500 == round(tours/2500) && vitesse < vitesseMax ) { 
      ////Accéléeration du moteur
      vitesse = vitesse+50; moteur.setSpeed(vitesse); 
      Serial.print  ("Nouvelle vitesse fixée à "); 
      Serial.println(vitesse);  
    }
    ////Fin de course atteinte, on met un terme au movement.
    if ((digitalRead(pinSW2) == LOW && libre == "ouvrons") || (digitalRead(pinSW1) == LOW && libre == "fermons")) {libre = "oui"; } 
    moteur.step(sens * pas);
    delay(10);
    tours=tours+1;
  }

  //Mise au repos du moteur  
  digitalWrite(pinMO1, LOW);
  digitalWrite(pinMO2, LOW);
  digitalWrite(pinMO3, LOW);
  digitalWrite(pinMO4, LOW);

  //Indication de l'état du verrou
  if (digitalRead(pinSW1) == HIGH) {
    ////La porte peut être ouverte
    digitalWrite(pinDER, LOW);
    digitalWrite(pinDEV, HIGH);
    Serial.println("Porte déverrouillée; entrez!");
  }
  if (digitalRead(pinSW2) == HIGH) {
    ////La porte est verrouillée
    digitalWrite(pinDER, HIGH);
    digitalWrite(pinDEV, LOW);
    Serial.println("Porte verrouilée; partez l`esprit tranquille, car votre porte est sécurisée.");
  }
  delay(1900);
  digitalWrite(pinDER, LOW);
  digitalWrite(pinDEV, LOW);
  digitalWrite(pinDEB, LOW);
  codeEntree = "";
  libre = "oui";
}


bool carteValide(byte *buffer, byte bufferSize) {
  String pat = "";
  for (byte i = 0; i < bufferSize; i++) {
    pat = pat + String(buffer[i] < 0x10 ? " 0" : " ");
    pat = pat + String(buffer[i], HEX);
  }
  pat.toUpperCase();
  pat.trim();
    //Serial.print(F("Remise à zéro des valeurs de carte magnétique:"));    //Dump UID
    for (byte i = 0; i < cartes.uid.size; i++) {
      Serial.print(cartes.uid.uidByte[i] < 0x10 ? " 0" : " ");
      Serial.print(cartes.uid.uidByte[i], HEX);
      cartes.uid.uidByte[i] = 0;
    }
  return (pat=="89 A3 F0 97") ?  true : false;
}

bool rien() {
  bool retour = true;
  if (digitalRead(pinCLA2) != digitalRead(pinCLA1)) { retour = false; 
    //Serial.println("1 et 2 différents");
  }
  if (digitalRead(pinCLA3) != digitalRead(pinCLA1)) { retour = false; 
    //Serial.println("1 et 3 différents");
  }
  if (digitalRead(pinCLA4) != digitalRead(pinCLA1)) { retour = false; 
    //Serial.println("1 et 4 différents");
  }
  if (digitalRead(pinCLA5) != digitalRead(pinCLA1)) { retour = false; 
    //Serial.println("1 et 5 différents");
  }
  if (digitalRead(pinCLA6) != digitalRead(pinCLA1)) { retour = false; 
    //Serial.println("1 et 6 différents");
  }
  if (digitalRead(pinCLA7) != digitalRead(pinCLA1)) { retour = false; 
    //Serial.println("1 et 7 différents");
  }
  if (digitalRead(pinCLA8) != digitalRead(pinCLA1)) { retour = false; 
    //Serial.println("1 et 8 différents");
  }
//  Serial.print  ("Après vérification de l`uniformité des valeurs, nous concluons ainsi: ");
//  Serial.println(retour);
  return retour;
}

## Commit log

2024-11-14 Code Arduino
2024-11-14 Impression 3d
    [Motorisation_Barrure_v2-Boulon.stl, Motorisation_Barrure_v2-Butoir.stl, Motorisation_Barrure_v2-Curseur.stl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]
2024-11-14 Update README.md
    Ajout de mon image
2024-11-15 Bibliothèques
    [Arduino-Uno-r3-with-RFID-RC522.fzz]
2024-11-17 plus dans doc 3 pico réduit
2024-11-17 plus dans doc 3 pico réduita
2024-11-17 plus dans doc 3 pico réduitb
2024-11-17 plus dans doc 3 pico réduitc
2024-11-17 plus dans doc 3 pico réduitd
2024-12-12 Une image de plus
2024-12-12 Réduction des images
2024-12-12 Changement de nom image
2024-12-12 Début de la page 4
2024-12-12 Correction de la destination Tuto/wiki
2024-12-12 Correction de la destination Tuto/wiki 2
2024-12-25 Correction de boucles
2025-11-15 lien vers fichiers 3d - correction des liens
2025-11-15 lien vers fichiers 3d - correction des liens sans blob
2025-11-15 lien vers fichiers 3d - correction des liens vers rép.
2025-11-15 Mise à jour des liens
2025-11-15 Lien vers arduino.cc
2025-11-15 Lien vers arduino.cc bis
2025-11-15 Images de la mécanique
2025-11-15 video de la mécanique
2025-11-15 Amélioration des images
